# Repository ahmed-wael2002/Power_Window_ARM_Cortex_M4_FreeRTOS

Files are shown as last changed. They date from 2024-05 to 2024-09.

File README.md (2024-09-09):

# Power Window Control System

### 🚗 Project Overview
This project showcases a **Power Window Control System** designed for modern vehicles using the **Tiva C microcontroller** and **FreeRTOS**. The system is scalable, configurable, and integrates various functionalities such as manual and automatic window control, obstacle detection, and safety features. It ensures compatibility across different vehicle models.

### ✨ Key Features
- **Manual & Automatic Control:**
  - **Manual Mode:** Continuous press for precise window control.
  - **Automatic Mode:** One-touch for full open/close functionality.
- **Driver and Passenger Control Board:**
  - Provides window control from driver control board (higher priority) or passenger control board.
- **Window Lock Function:**
  - Locks all windows except the driver's for enhanced security.
- **Jam Protection:**
  - Detects obstacles during the one-touch auto-close operation then retreats the window for safety.
- **Highly Configurable:**
  - Provides manual configuration through MACROS for adapting the project into any hardware architecture.
- **Templates:**
  - Provides sample demo project for easier integration.

 ---

### ✨ Technologies Used
- FreeRTOS (Project built on ARM Keil)
- TM4C123GH6PM (Tiva C Launchpad - ARM Cortex M4)

---

### 🛠️ System Architecture
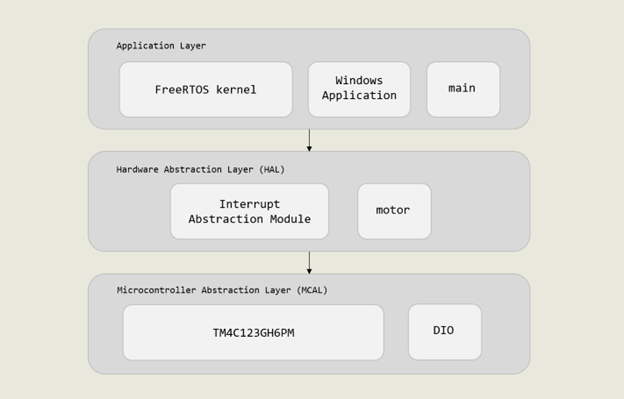
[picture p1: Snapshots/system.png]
System Diagram


---

### 🔧 Configuration
1- Edit the system configurations in Windows.h (Passenger Control GPIO - Driver Control GPIO - Motor GPIO - etc.) as illustrated in the following screenshot.
2- Rebuild the system.
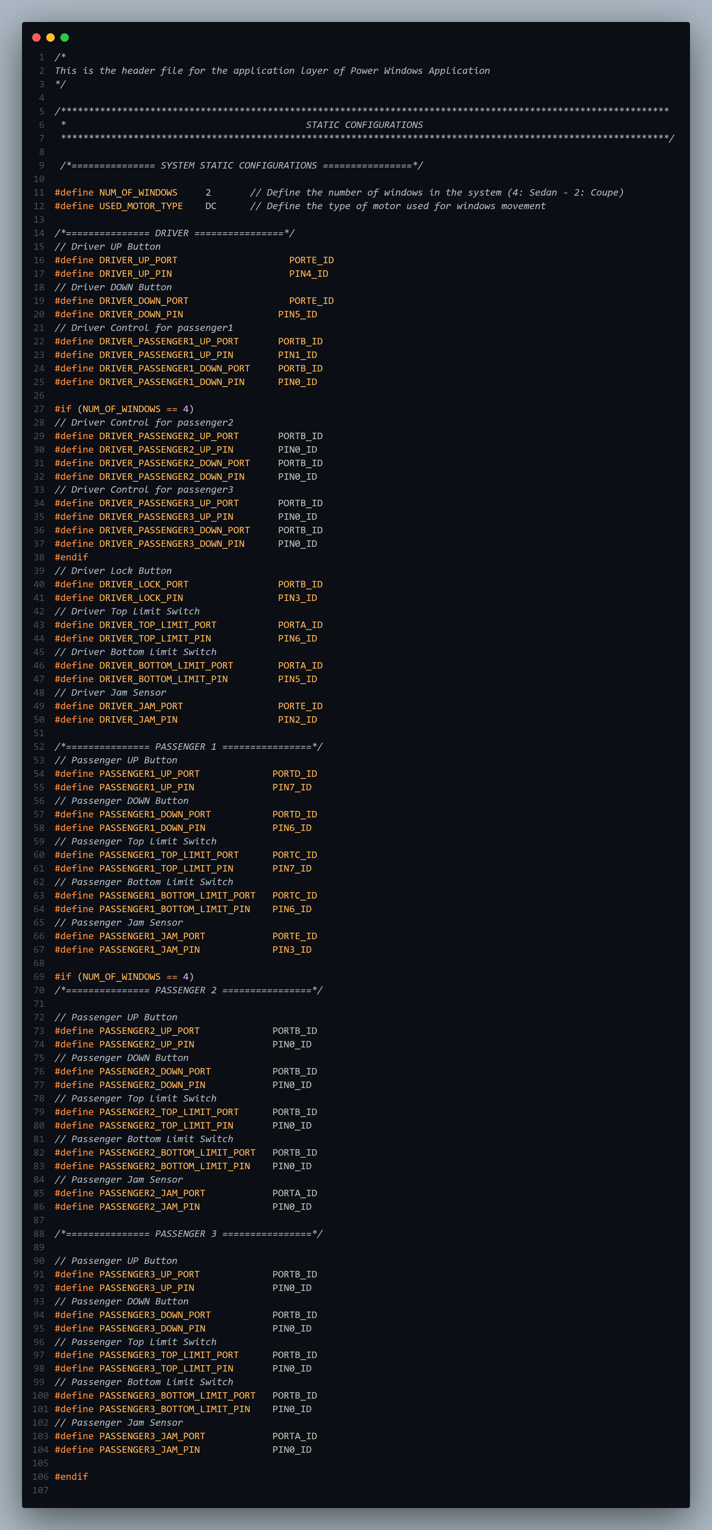
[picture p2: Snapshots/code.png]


--- 

### 📂 Additional Resources
- **[📹 Video Demonstration & Documentation](https://drive.google.com/file/d/1O1Iedp_n3LcsQSbOaQz3eCcksW22hzNp/view?usp=sharing)**
- **[💻 GitHub Repository](https://github.com/ahmed-wael2002/Power_Window_ARM_Cortex_M4_FreeRTOS)**

For more detailed documentation and code examples, visit the [GitHub repository](https://github.com/ahmed-wael2002/Power_Window_ARM_Cortex_M4_FreeRTOS).

---

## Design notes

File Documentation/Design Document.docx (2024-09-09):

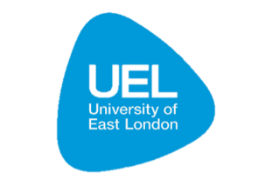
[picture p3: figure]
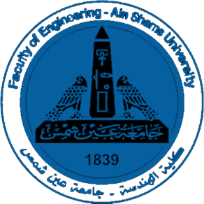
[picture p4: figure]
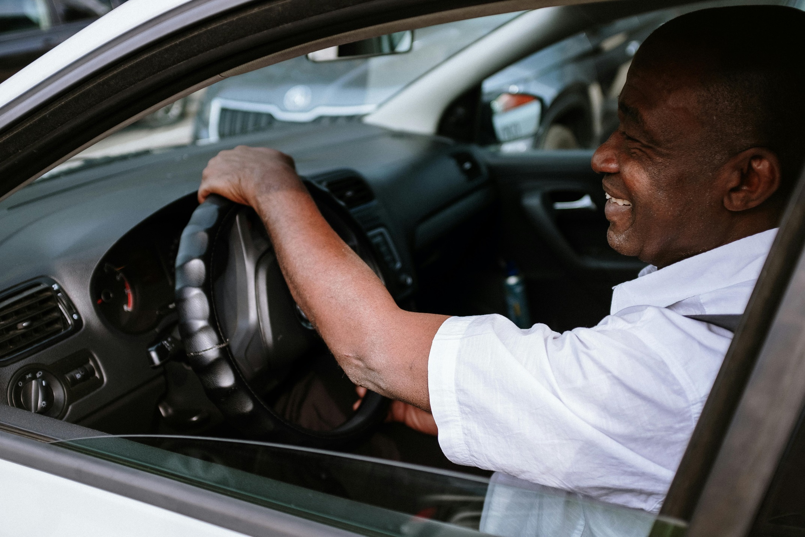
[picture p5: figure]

POWER WINDOW CONTROL SYSTEM using Tiva C running FreeRTOS

Real-time and Embedded Systems Design- CSE411

Submitted to

Prof. Sherif Hammad - Eng. Ayman Baharia

Team: 21

Ahmed Wael Ibrahim Mohamed | 20P3343
Mustafa Usama Abdelrahman | 20P5556
Ahmed Sameh Mahmoud Nabieh | 20P2914
Farah Ahmed Abdelrehim Tharwat | 20P1269
Salma Mohamed Elsoly | 20P6375

# List of Figures

Table 1: Sample main function 7

Project files, video demonstration and Documentation in rar file format:

https://drive.google.com/file/d/1O1Iedp_n3LcsQSbOaQz3eCcksW22hzNp/view?usp=sharing

Github Repository of the project:

ahmed-wael2002/Power_Window_ARM_Cortex_M4_FreeRTOS (github.com) (https://github.com/ahmed-wael2002/Power_Window_ARM_Cortex_M4_FreeRTOS)

# Introduction

In the realm of modern vehicle technology, the Power Window Control System stands out as a pivotal component, elevating passenger convenience and safety. Our endeavor centers on crafting a versatile system capable of seamless integration with a spectrum of vehicle systems. Utilizing the Tiva C microcontroller platform and fortified with the scalability of FreeRTOS for task management, our focus lies on developing a solution that is both generic and adaptable. This approach aims to ensure compatibility across different vehicle models, ultimately enhancing the overall passenger experience.

## Project Scope

The primary objectives of our project are as follows:

1. Front Passenger Door Window Implementation: We aim to create a reliable and generic power window system for passengers and driver windows. Both the passenger and driver control panels will have seamless access to window operation.
2. Power Window (Manual and Automatic Functionalities): We aim to provide manual and automatic window movement function with the utilization of simple push-buttons or any cheap available switches.
3. Generic System: We aim to build a configurable, generic and scalable system conforming to industry standards, helping the software system to be installed on different vehicle systems of different designs.
4. FreeRTOS Integration: We aim to build the system over FreeRTOS open-source kernel, to leverage and demonstrate the power of parallelized tasks execution.
5. Limit Switch Implementation: To ensure safe window operation, we will incorporate two limit switches. These switches will prevent the window motor from exceeding the top and bottom limits of the window frame.
6. Obstacle Detection: While a current stall sensor is unnecessary, we will employ a simple push-button mechanism to detect obstructions. If an obstacle is detected during the one-touch auto-close operation, the system will halt the window movement within 0.5 seconds.

## System Basic Features

Our power window control system will offer the following features:

1. Manual Open/Close Function:
  - When the power window switch is continuously pushed or pulled, the window will open or close until the switch is released.
  - This feature provides flexibility for precise window positioning.
2. One-Touch Auto Open/Close Function:
  - A short press of the power window switch will fully open or close the window.
  - Passengers can effortlessly adjust the window position without continuous input.
3. Window Lock Function:
  - Enabling the window lock switch will disable the opening and closing of all windows except the driver’s window.
  - Enhances security and prevents accidental window adjustments by passengers.
4. Jam Protection Function:
  - In case foreign matter obstructs the window during one-touch auto-close operation, the system will automatically stop the window.
  - Within 0.5 seconds, the window will move downward slightly to release the obstruction.

# System Architecture

## Software Components Layout

Our project utilized the industry standard layered architecture as illustrated in the following figure.

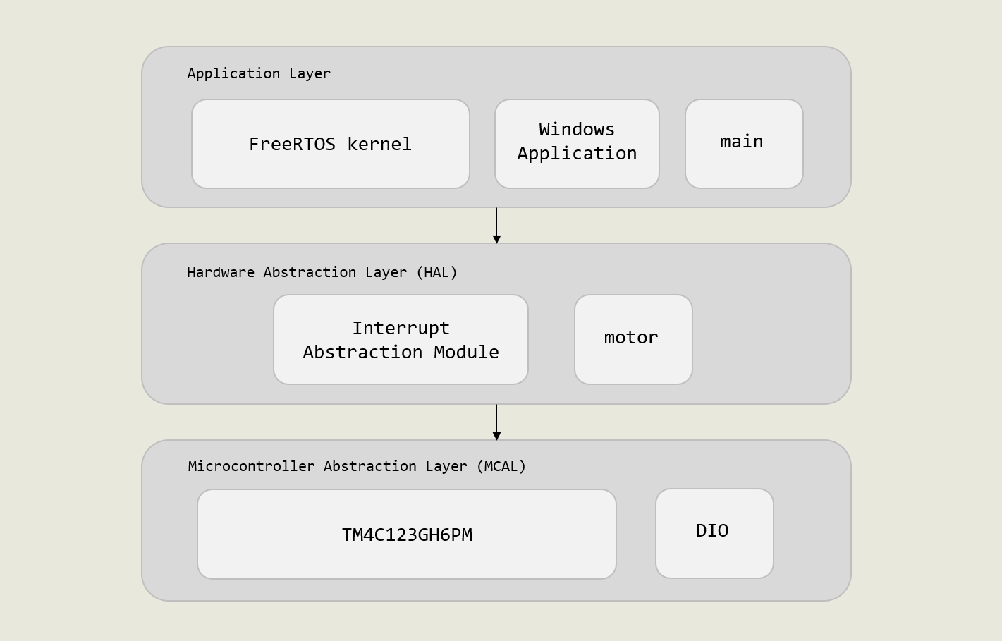
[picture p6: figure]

Figure 1: Layered Architecture Implementation

Application Layer

This is the layer wrapping the actual application code used for building the system. This layer comprises of: FreeRTOS Kernel files, Windows.h header files and main.c main function.

To create a scalable, modular and layered system, windows tasks definitions and functions are declared in a separate software module called windows.h, the main objective is to define the system and task definitions that are loaded into the FreeRTOS kernel for parallel execution. The windows module will be further explained in a later section in this document.

The main.c module initializes the FreeRTOS scheduler, system modules then loads the task definitions into the FreeRTOS application.

Hardware Abstraction Layer

In this layer, we have implemented generic software modules that interface with the underlying hardware components needed for the windows operation: motors and interrupt modules. It is worth noting that the motor driver module is built based on L298N H-bridge Motor Control Board that interfaces with DC Motors. A software modification might be required to re-interface with Stepper motors or any other kind of motors.

## FreeRTOS Tasks Structure

The system was structured with an object-oriented mindset. The system integrator must firstly define the number of windows present in the vehicle then adjust the corresponding static configurations in windows.h header file, this maintains system scalability where the system will define a set of generic parameterized window tasks whose number corresponds to the actual hardware requirements.

In the following diagram, the tasks are divided into: Window Control Tasks, Motor Task and Jamming Tasks. The system integrator can instantiate any number of generic Passenger tasks as will be explained in Window Task, but only 1 Motor and 1 Semaphore Jamming tasks can be instantiated. The motor and jamming tasks were built in a generic form to reduce the overhead of creating multiple tasks for multiple window control panels which might introduce a performance bottleneck in the system.

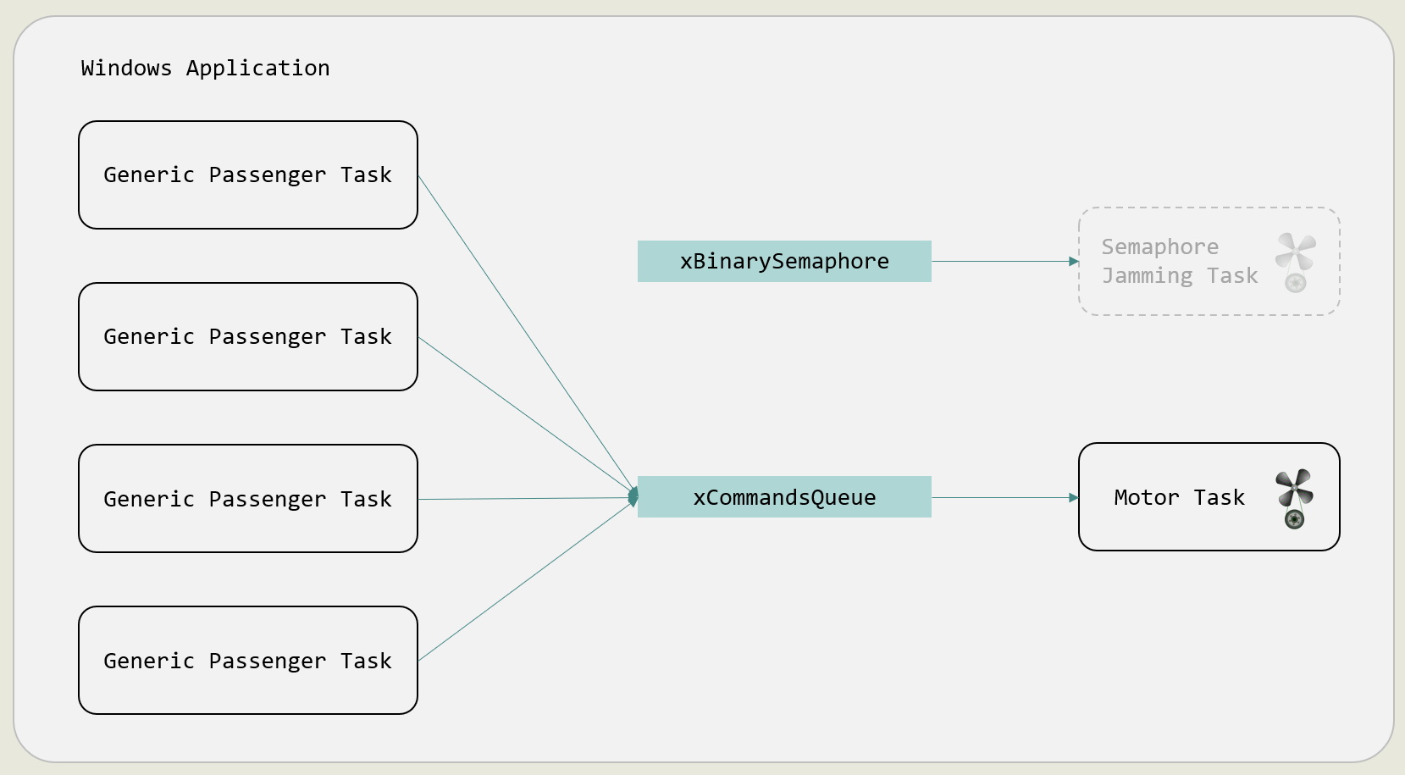
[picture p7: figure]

Figure 2: FreeRTOS Tasks Structure

### Window Task

This is a generic window control task responsible for handling user inputs from the window control panel. The task is generic meaning that the tasks is only defined once but is instantiable to any number of times corresponding to the static configuration “NUM_OF_WINDOWS” found in windows.h. Preferably, this configuration could be NUM_OF_WINDOWS = 2 or 4 to conform to standard vehicle designs.

The task parameters is sent as a structure comprising the necessary input controls GPIO ports and pins, as illustrated in the following snapshot.

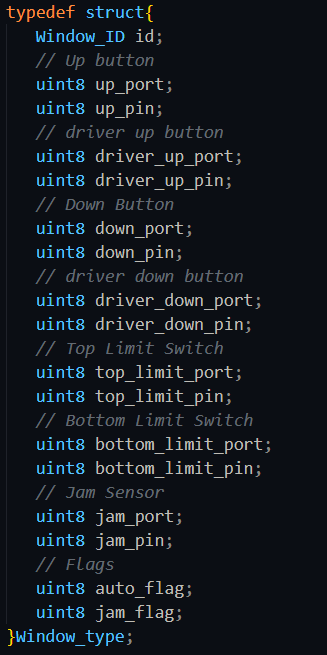
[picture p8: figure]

- Window_id: Is an enumeration used to identify window task, as an example (Driver Task has the id: 0, while Passenger1 Task has the id: 1).
- GPIO ports: These are a group of 8-bit variables that identify the GPIO pin corresponding to each panel input.
- auto_flag, jam_flag: These are Boolean flags used to identify the automatic state of the system and facilitate the jamming operation.

This parameter structure approach facilitates building decoupled tasks, meaning system integrators nor developers are required to define additional functions in the system to add hardware components.

In this sense, the system initialization simply initializes the GPIO pins for panels and fills the structure, an the user can instantiate multiple task functions only by appropriate construction of the parameters.

To automate the task initialization for system integrators, a public array of windows is defined in windows.h and can be externed in the main function to only interate through the array and create a corresponding task as illustrated in the following code example.

Table 1: Sample main function

// Variables are externed from module -- Check for documentation

extern Window_type windows[NUM_OF_WINDOWS];

extern QueueHandle_t xCommandQueue;

extern xSemaphoreHandle xBinarySemaphore;

int main( void )

{

// Initializing Windows GPIO

WINDOW_init();

// Initializing commands queue

xCommandQueue = xQueueCreate(20, sizeof(uint8_t));

// Initializing binary semaphore

vSemaphoreCreateBinary(xBinarySemaphore);

if (xBinarySemaphore != NULL){

// Semaphore is created successfully

for (uint8 i=0; i<NUM_OF_WINDOWS; i++){

// Create Passenger Task (PASSENGER1, PASSENGER2, PASSENGER3

xTaskCreate(

WINDOW_PassengerTask,

"Window Task",

300,

(void *)&windows[i],

1,

NULL

);

}

// Create Motor Task

xTaskCreate(

WINDOW_MotorTask,

"Window Task",

300,

NULL,

1,

NULL

);

// Create jamming semaphore task of higher priority

xTaskCreate(

WINDOW_JammingSemaphoreTask,

"Window Task",

300,

NULL,

3,

NULL

);

// Start the scheduler and run tasks

vTaskStartScheduler();

}

/* If all is well we will never reach here as the scheduler will noe

be running the tasks. If we reach here then it is likely that there was

insufficient heap memory available for a resource to be created */

for(;;);

}

The windows task main aim is to read the user’s input by reading the GPIO pins declared in the parameter structure, process the inputs to define the operation to be executed then communicate a command to the motor task to move interface with the motor hardware. The task communication process is further explained in the Commands and Queues section.

The following features are implemented in this module as follows:

- Manual Control: the GPIO pin is read then vTaskDelay() is called to wait for a specific period of time, then re-read the GPIO pin. A post-delay ON reading on the GPIO pin indicates the user’s continuous press on the switch triggering the manual movement of the windows. It is worth noting that the jamming operation is only accounted for in the automatic operation as defined in the design specifications document.
- Automatic Control: As opposed to Manual Control operation, a post-delay OFF reading indicates the user’s one-touch press which triggers the automatic movement of the windows.
- xQueueSend: The operation command is pushed into the commands queue to be continuously read by the motor task for execution.
- Driver-to-passenger Control: In the parameter structure, a corresponding driver_up_GPIO and driver_down_GPIO where they are also read in the generic task, however, the reading operation is conditional, meaning, it can only be read, if the private global variable g_isLocked is on, in other words, the driver locked the windows operations. This makes the windows only controllable by the driver in case of locked state.
- Limit Switches: Limit switches GPIO parameters set a group of conditions that resets the task operation and force it to send a Motor_stop command to the motor task.

### Motor Task

The motor task simple continuously receives from the commands queue task commands, decodes the commands then call the corresponding function from the motor driver module to interface with the hardware.

### Commands and Queues

A queue is defined to create a communication channel between the window control tasks and the motor tasks to help send/receive commands and execute operations.

The following code snapshot illustrates the basic commands defined in the system (Command definitions can be found in the Operational Macros section in windows.h).

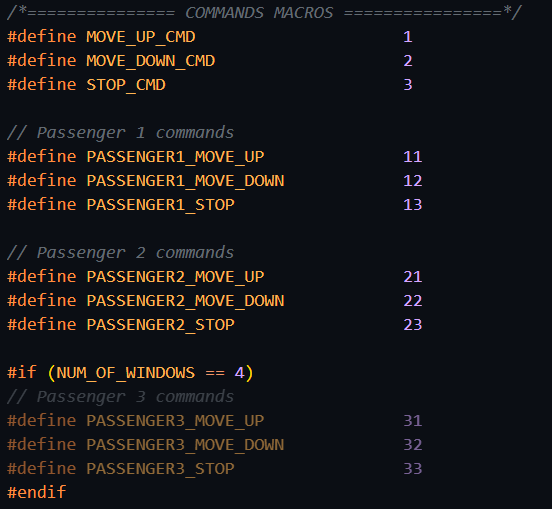
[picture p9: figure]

As discussed in the Window Task section, a reduction in the tasks creation overhead is achieved by creating a single generic Motor task. This is achieved by creating a commands protocol which the motor task could decode and understand which motor to be activated and with which operation.

As discussed also, the parameter structure contain a window_id, which can be used to identify the target motor hardware, our implementation of the command is simple and goes as follows:

command=(window id*10)+command

For example, the command for triggering PASSENGER2 windows of id=2 to move upwards would be as follows:

pass2 move up cmd=(2*10)+1=21

### Semaphores and Jamming

Jamming is considered a safety-critical issue whose priority exceeds all operations of the system, consecutively, the implementation of jamming operation is done using a higher-priority task that directly controls the motors and have access to windows array.

Referring to Figure 2: FreeRTOS Tasks Structure the Jamming task is initially blocked as the semaphore is not given, until the Jamming_ISR defined in windows.c toggles the jam_flag in a corresponding windows array element, after wise, the ISR gives the semaphore to the Jamming task then forces context switching.

The semaphore task then iterates through the array of windows till it finds a window object whose jam_flag is on, it then assesses the auto_flag which is only raised in case of automatic move up operation. If both flags are raised, the Jamming task forces the motor to move in the opposite direction for a statically configured JAM_DELAY_MS then stops the motor. It is worth noting that the Jamming task also checks for bottom_limit_switches to avoid moving the window outside its boundaries. The following code snapshots showcase the implementation of the semaphore task and ISR.

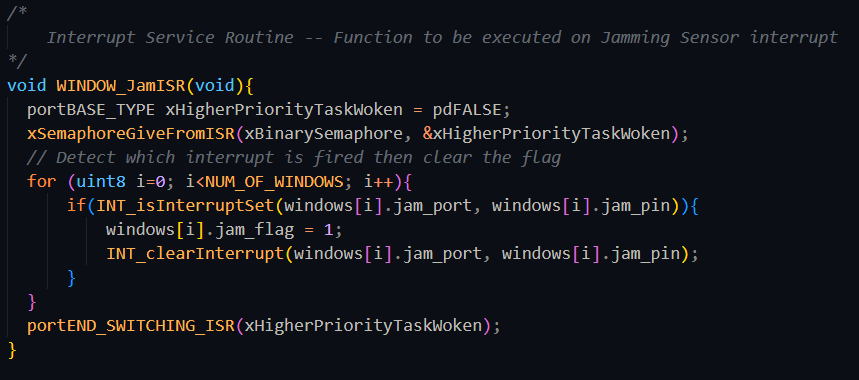
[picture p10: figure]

Figure 3: Jam Interrupt Service Routine

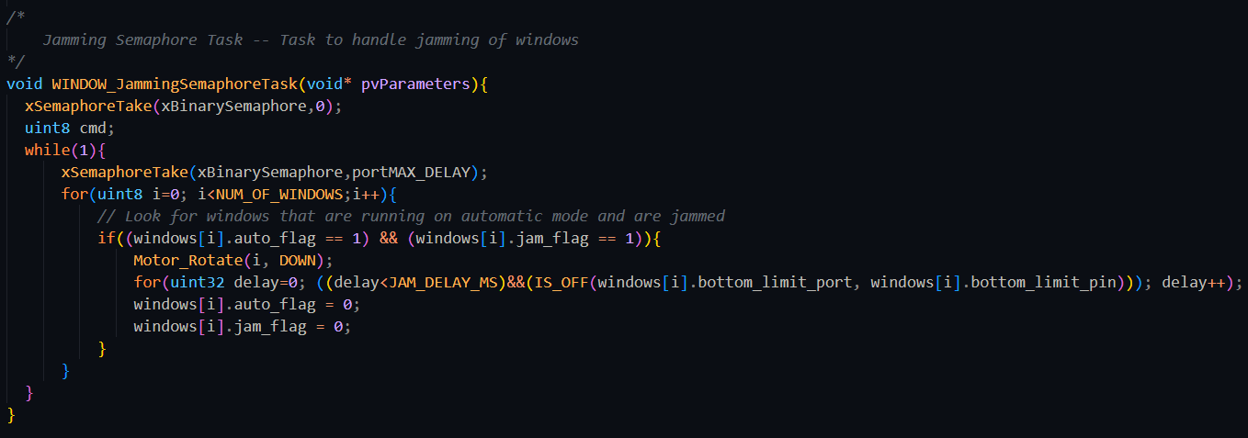
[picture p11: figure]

Figure 4: Jamming semaphore task implementation

# Demonstration

## Hardware Items List

Item Image | Item Name/Code | Functionality

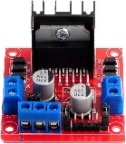
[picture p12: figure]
L298N Motor Drive Controller Board Module Dual H Bridge DC Stepper ForArduino Smart Car Robot UNO MEGA R3 MEGA 2560 ESP32 ESP826

| Dual H-Bridge Motor Driver | Hardware control board that bridges and facilitates the connection of the DC motors with Tiva C board

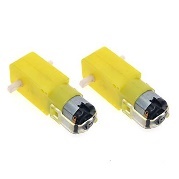
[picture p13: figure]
Mini DC Gearbox Motors Pair (2 Motors) With Back Shaft

| Mini DC Gearbox Motors with Back Shaft | DC Motors used to move windows in both directions, a gearbox is used to reduce the RPM speed of motors with no software intervention

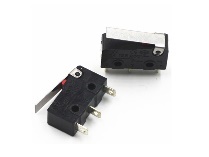
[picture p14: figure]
Micro Switch - MS2

| Micro Limit Switches | Used to signal whether the window reached the maximum height limit or the maximum depth limit

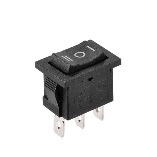
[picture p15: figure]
SW4 - ON/OFF/ON Switch 3 pin

| 3-level Rocker Switch | Used in the window control panel to signal up/down commands

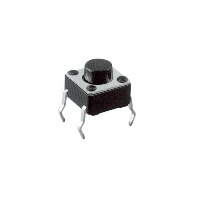
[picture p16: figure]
Press 4pin 6x6x4.5 mm Tack Switch

| Push button | Used to emulate GPIO input for Jamming Stall Sensors

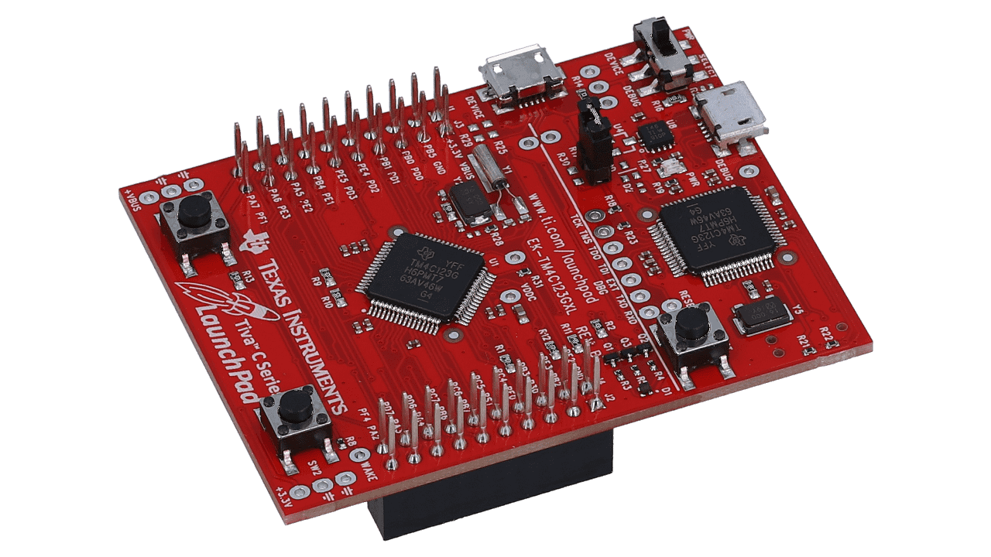
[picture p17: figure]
EK-TM4C123GXL Evaluation board | TI.com

| Tiva C Launchpad | Arm Cortex M4 – based microcontroller

## Circuit Wiring

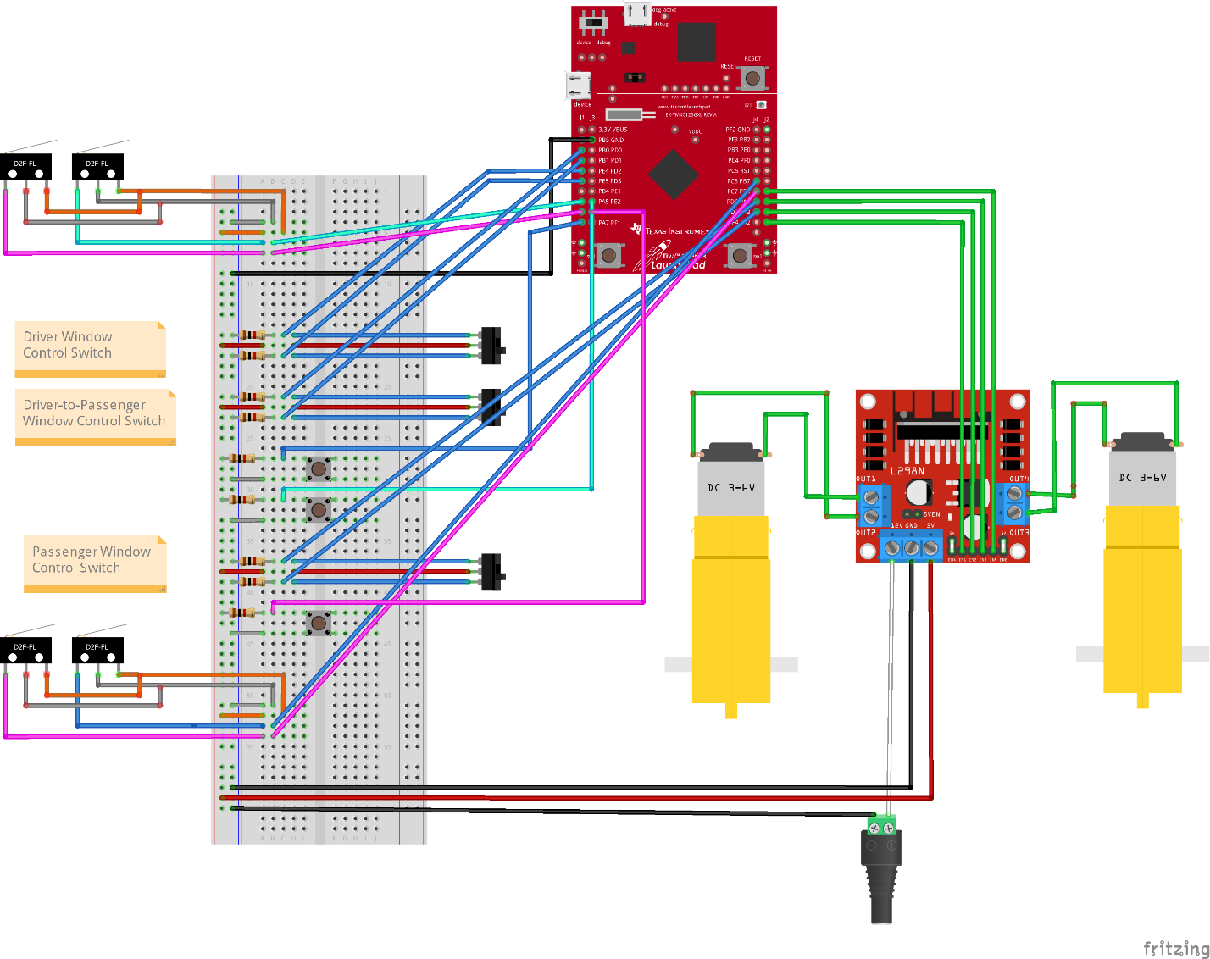
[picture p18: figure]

Figure 5: Demo project circuit wiring using Fritzing

## Software System Integration

System Configurations are adjusted in the statics configurations section in windows.h header file as follows

1. Firstly, adjust NUM_OF_WINDOWS = 2. In this demo project we will use the 2-seat vehicle design with only 1 Driver and 1 Passenger Control panels.
2. Adjust all ports and pins accordingly
3. Use the code sample in Window Task section.

The following are the static configurations used in the demo project.

/*=============== SYSTEM STATIC CONFIGURATIONS ================*/

#define NUM_OF_WINDOWS 2 // Define the number of windows in the system (4: Sedan - 2: Coupe)

#define USED_MOTOR_TYPE DC // Define the type of motor used for windows movement

/*=============== DRIVER ================*/

// Driver UP Button

#define DRIVER_UP_PORT PORTE_ID

#define DRIVER_UP_PIN PIN4_ID

// Driver DOWN Button

#define DRIVER_DOWN_PORT PORTE_ID

#define DRIVER_DOWN_PIN PIN5_ID

// Driver Control for passenger1

#define DRIVER_PASSENGER1_UP_PORT PORTB_ID

#define DRIVER_PASSENGER1_UP_PIN PIN1_ID

#define DRIVER_PASSENGER1_DOWN_PORT PORTB_ID

#define DRIVER_PASSENGER1_DOWN_PIN PIN0_ID

// Driver Lock Button

#define DRIVER_LOCK_PORT PORTB_ID

#define DRIVER_LOCK_PIN PIN3_ID

// Driver Top Limit Switch

#define DRIVER_TOP_LIMIT_PORT PORTA_ID

#define DRIVER_TOP_LIMIT_PIN PIN6_ID

// Driver Bottom Limit Switch

#define DRIVER_BOTTOM_LIMIT_PORT PORTA_ID

#define DRIVER_BOTTOM_LIMIT_PIN PIN5_ID

// Driver Jam Sensor

#define DRIVER_JAM_PORT PORTE_ID

#define DRIVER_JAM_PIN PIN2_ID

/*=============== PASSENGER 1 ================*/

// Passenger UP Button

#define PASSENGER1_UP_PORT PORTD_ID

#define PASSENGER1_UP_PIN PIN7_ID

// Passenger DOWN Button

#define PASSENGER1_DOWN_PORT PORTD_ID

#define PASSENGER1_DOWN_PIN PIN6_ID

// Passenger Top Limit Switch

#define PASSENGER1_TOP_LIMIT_PORT PORTC_ID

#define PASSENGER1_TOP_LIMIT_PIN PIN7_ID

// Passenger Bottom Limit Switch

#define PASSENGER1_BOTTOM_LIMIT_PORT PORTC_ID

#define PASSENGER1_BOTTOM_LIMIT_PIN PIN6_ID

// Passenger Jam Sensor

#define PASSENGER1_JAM_PORT PORTE_ID

#define PASSENGER1_JAM_PIN PIN3_ID

A system integrator can scale up the demo project by changing the value NUM_OF_WINDOWS macro to 4 then adjust the appropriate configurations for the GPIO pins.

In addition, one can use the sample code as the main code to initialize tasks and system hardware enlisted in Table 1: Sample main function.

2 Real-time and Embedded Systems Design – CSE411

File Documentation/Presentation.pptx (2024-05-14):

## Power window using freeRTOS

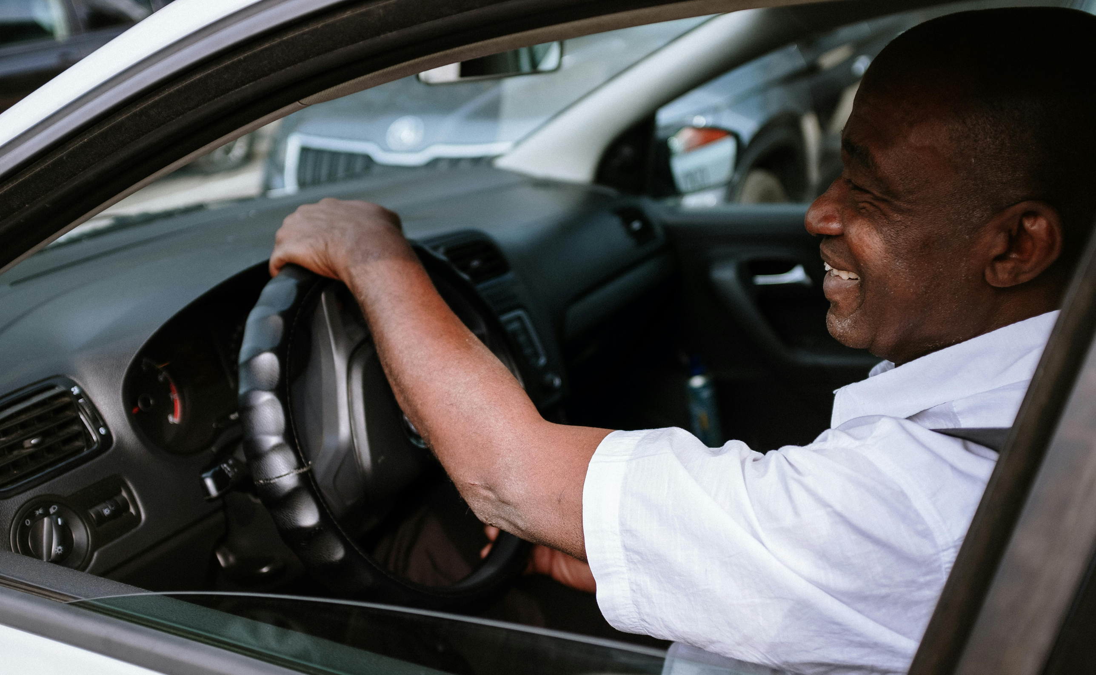
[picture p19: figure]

## Team 21

Ahmed Wael Ibrahim – 20P3343
Mustafa Usama Abdelrahman – 20P5556
Ahmed Sameh Mahmoud Nabieh – 20P2914
Farah Ahmed Abdelrehim Tharwat – 20P1269
Salma Mohamed Elsoly – 20P6375

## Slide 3

Application Layer

Hardware Abstraction Layer (HAL)

FreeRTOS kernel

Windows Application

main

Interrupt Abstraction Module

motor

Microcontroller Abstraction Layer (MCAL)

TM4C123GH6PM

DIO

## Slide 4

Windows Application

Generic Passenger Task

Semaphore Jamming Task

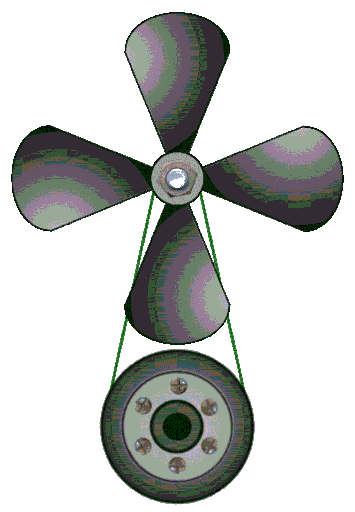
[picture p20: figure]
Propeller Motor Air - Free GIF on Pixabay - Pixabay

Generic Passenger Task

xBinarySemaphore

Generic Passenger Task

Motor Task

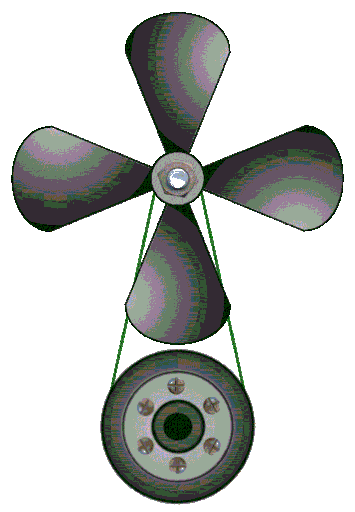
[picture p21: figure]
Propeller Motor Air - Free GIF on Pixabay - Pixabay

xCommandsQueue

Generic Passenger Task

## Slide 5

Windows Application

Generic Passenger Task

Semaphore Jamming Task

Generic Passenger Task

xBinarySemaphore

Generic Passenger Task

Motor Task

xCommandsQueue

Generic Passenger Task

## Code implementation

## Demo project

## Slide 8

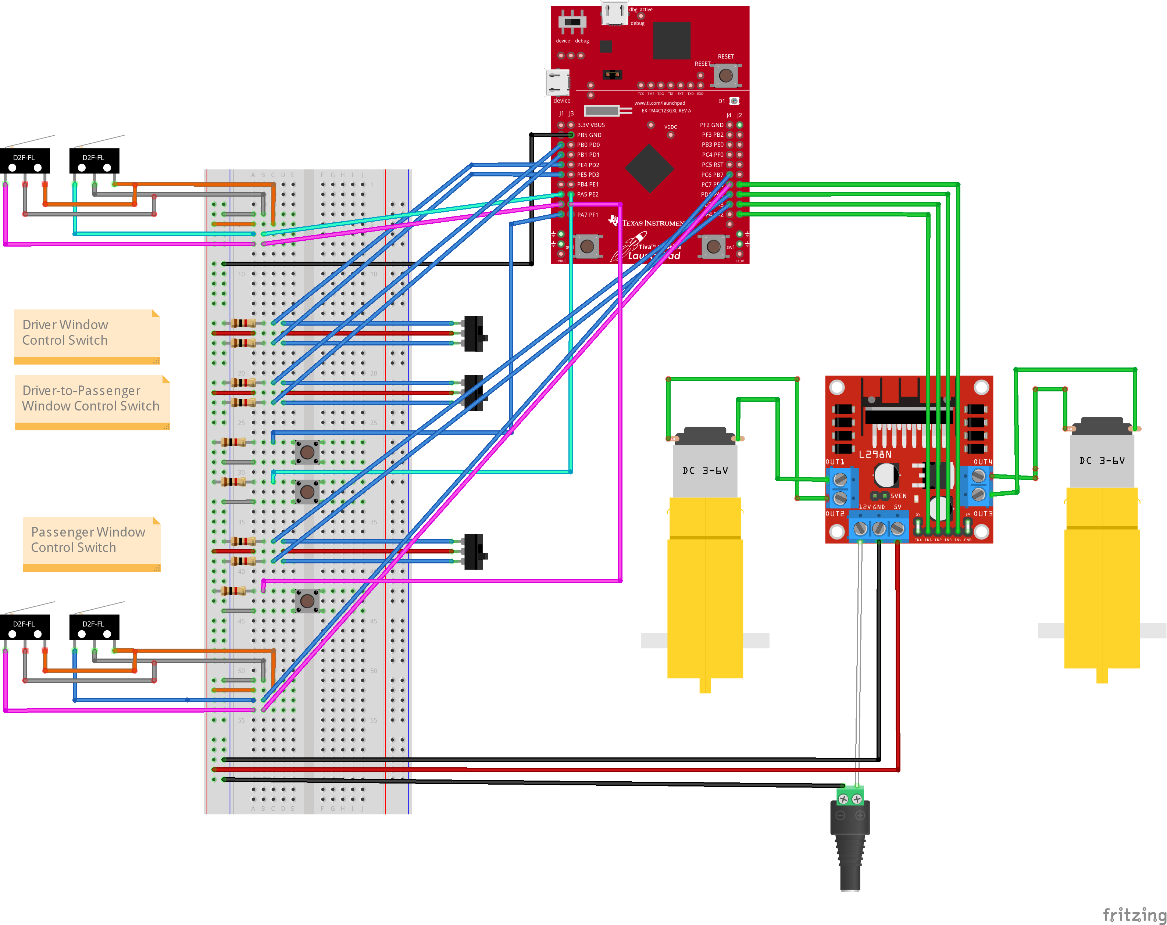
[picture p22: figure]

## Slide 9

- Two panels are installed to control the passenger’s window?
- FreeRTOS is used in the project implementation?
- Implementation of 2 limit switches to limit the window motor from top and bottom limits of the window?
- When the power window switch is pushed or pulled continuously, the window opens or closes until the switch is released?
- When the power window switch is pushed or pulled shortly, the window fully opens or closes?
- When the window lock switch is turned on, the opening and closing of all windows except the driver’s window is disabled?
- Jam Protection is implemented?
- Queues are used in the project implementation?
- Semaphores/Mutex are used in the project implementation?
- Documentation project is made?

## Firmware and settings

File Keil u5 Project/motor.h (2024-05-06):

/*
 * motor.h
 *
 *  Created on: Apr 24, 2024
 *      Author: Ahmed Wael
 */

#ifndef MOTOR_H_
#define MOTOR_H_

#include "types.h"
#include "DIO.h"

/* 
This is header file declares a set of functions to control 2 DC motors 
by interfacing with L298N Motor Driver Module which allows simultaneous control of 2 motors.
The driver module is controlled by 3 pins:
1- Enable 1 pin: to enable the first motor
2- Input 1,2 pins: Control the rotation direction of the first motor
3- Enable 2 pin: to enable the second motor
4- Input 3,4 pins: Control the rotation direction of the second motor
*/

/*************************************************************************************************************
  			                                MACROS DEFINITIONS
 *************************************************************************************************************/

/*=============== SYSTEM STATIC CONFIGURATIONS ================*/
#define NUM_OF_MOTORS		2
#define TYPE_OF_MOTORS		DC


/*=============== OPERATIONAL MACROS ================*/





/*=============== MOTORS GPIO ================*/

/* Defining Enable pin for Motor
 * In case of a variable speed driver:
 * 	This pin should be connected to timer PWM output pin
 */

// Controlling First Motor
#define MOTOR1_EN_PORT 		PORTA_ID
#define MOTOR1_EN_PIN 		PIN4_ID
#define MOTOR1_IN1_PORT 	PORTA_ID
#define MOTOR1_IN1_PIN 		PIN2_ID
#define MOTOR1_IN2_PORT 	PORTA_ID
#define MOTOR1_IN2_PIN 		PIN3_ID

// Controlling Second Motor
#define MOTOR2_EN_PORT 		PORTD_ID
#define MOTOR2_EN_PIN 		PIN6_ID
#define MOTOR2_IN1_PORT		PORTA_ID
#define MOTOR2_IN1_PIN		PIN4_ID
#define MOTOR2_IN2_PORT		PORTB_ID
#define MOTOR2_IN2_PIN		PIN6_ID

#if (NUM_OF_MOTORS == 4)
// Controlling Third Motor
#define MOTOR3_EN_PORT 		PORTB_ID
#define MOTOR3_EN_PIN 		PIN3_ID
#define MOTOR3_IN1_PORT 	PORTB_ID
#define MOTOR3_IN1_PIN 		PIN0_ID
#define MOTOR3_IN2_PORT 	PORTB_ID
#define MOTOR3_IN2_PIN 		PIN1_ID

// Controlling Fourth Motor
#define MOTOR4_EN_PORT 		PORTB_ID
#define MOTOR4_EN_PIN 		PIN4_ID
#define MOTOR4_IN1_PORT		PORTD_ID
#define MOTOR4_IN1_PIN		PIN0_ID
#define MOTOR4_IN2_PORT		PORTD_ID
#define MOTOR4_IN2_PIN		PIN1_ID
#endif

/******************************************
 * 			 TYPES DEFINITIONS
 ******************************************/
/*
 * This enum is used to define the direction of rotation of the motor
 * 1- OFF			: IN1=0, IN2=0
 * 2- ANTICLOCKWISE	: IN1=0, IN2=1
 * 3- CLOCKWISE		: IN1=1, IN2=0
 */
typedef enum{
	OFF,			/* 00 */
	ANTICLOCKWISE, 	/* 01 */
	CLOCKWISE		/* 10 */
}Motor_Direction;

typedef enum{
	MOTOR1,
	MOTOR2,
	MOTOR3,
	MOTOR4
}Motor_ID;


/******************************************
 * 			FUNCTION PROTOTYPES
 ******************************************/
void Motor_init(void);
void Motor_Rotate(Motor_ID motor, Motor_Direction direction);


#endif /* MOTOR_H_ */

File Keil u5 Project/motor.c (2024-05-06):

/*
 * motor.c
 *
 *  Created on: Apr 24, 2024
 *      Author: Wael
 */

 // This is a simple implementation for the motor driver
 // The Power Window project requirements only need constant rotation speed so PWM control will not be implemented
 // Such reduction is necessary to avoid unnecessary usage of timers and PWM controls
 // Ensure jumper is placed on the Enable pins to allow max speed operation

/****** PWM control can be added in future implementations calling for variable speed ******/

#include "motor.h"


/*
 * This function initializes the DC motors by setting up the direction and state of the motor pins.
 * It also ensures that all the motor pins are initially set to the off state.
 */
void Motor_init(void){
	// Motor 1 - inits
	//DIO_Init(MOTOR1_EN_PORT, MOTOR1_EN_PIN, PIN_OUTPUT);
	DIO_Init(MOTOR1_IN1_PORT, MOTOR1_IN1_PIN, PIN_OUTPUT);
	DIO_Init(MOTOR1_IN2_PORT, MOTOR1_IN2_PIN, PIN_OUTPUT);
	//DIO_writePin(MOTOR1_EN_PORT, MOTOR1_EN_PIN, LOGIC_LOW);
	DIO_writePin(MOTOR1_IN1_PORT, MOTOR1_IN1_PIN, LOGIC_LOW);
	DIO_writePin(MOTOR1_IN2_PORT, MOTOR1_IN2_PIN, LOGIC_LOW);
	
	// Motor 2 - inits
	//DIO_Init(MOTOR2_EN_PORT, MOTOR2_EN_PIN, PIN_OUTPUT);
	DIO_Init(MOTOR2_IN1_PORT, MOTOR2_IN1_PIN, PIN_OUTPUT);
	DIO_Init(MOTOR2_IN2_PORT, MOTOR2_IN2_PIN, PIN_OUTPUT);
	//DIO_writePin(MOTOR2_EN_PORT, MOTOR2_EN_PIN, LOGIC_LOW);
	DIO_writePin(MOTOR2_IN1_PORT, MOTOR2_IN1_PIN, LOGIC_LOW);
	DIO_writePin(MOTOR2_IN2_PORT, MOTOR2_IN2_PIN, LOGIC_LOW);
		
	#if (NUM_OF_MOTORS == 4)
	// Motor 3 - inits
	DIO_Init(MOTOR3_EN_PORT, MOTOR3_EN_PIN, PIN_OUTPUT);
	DIO_Init(MOTOR3_IN1_PORT, MOTOR3_IN1_PIN, PIN_OUTPUT);
	DIO_Init(MOTOR3_IN2_PORT, MOTOR3_IN2_PIN, PIN_OUTPUT);
	DIO_writePin(MOTOR3_EN_PORT, MOTOR3_EN_PIN, LOGIC_LOW);
	DIO_writePin(MOTOR3_IN1_PORT, MOTOR3_IN1_PIN, LOGIC_LOW);
	DIO_writePin(MOTOR3_IN2_PORT, MOTOR3_IN2_PIN, LOGIC_LOW);
	
	// Motor 4 - inits
	DIO_Init(MOTOR4_EN_PORT, MOTOR4_EN_PIN, PIN_OUTPUT);
	DIO_Init(MOTOR4_IN1_PORT, MOTOR4_IN1_PIN, PIN_OUTPUT);
	DIO_Init(MOTOR4_IN2_PORT, MOTOR4_IN2_PIN, PIN_OUTPUT);
	DIO_writePin(MOTOR4_EN_PORT, MOTOR4_EN_PIN, LOGIC_LOW);
	DIO_writePin(MOTOR4_IN1_PORT, MOTOR4_IN1_PIN, LOGIC_LOW);
	DIO_writePin(MOTOR4_IN2_PORT, MOTOR4_IN2_PIN, LOGIC_LOW);
	#endif
}

/*
 * This function rotates the DC motor in the specified direction.
 * It takes two parameters: the motor ID and the direction.
 * The motor ID can be either MOTOR1 or MOTOR2.
 * The direction can be OFF, ANTICLOCKWISE, or CLOCKWISE.
 */
void Motor_Rotate(Motor_ID motor, Motor_Direction direction){
	switch(motor){
		case MOTOR1:
			if (direction == OFF){
				DIO_writePin(MOTOR1_IN1_PORT, MOTOR1_IN1_PIN, LOGIC_LOW);
				DIO_writePin(MOTOR1_IN2_PORT, MOTOR1_IN2_PIN, LOGIC_LOW);
			}
			else if (direction == ANTICLOCKWISE){
				DIO_writePin(MOTOR1_IN1_PORT, MOTOR1_IN1_PIN, LOGIC_LOW);
				DIO_writePin(MOTOR1_IN2_PORT, MOTOR1_IN2_PIN, LOGIC_HIGH);
			}
			else if (direction == CLOCKWISE){
				DIO_writePin(MOTOR1_IN1_PORT, MOTOR1_IN1_PIN, LOGIC_HIGH);
				DIO_writePin(MOTOR1_IN2_PORT, MOTOR1_IN2_PIN, LOGIC_LOW);
			}
		break;

		case MOTOR2:
			if (direction == OFF){
				DIO_writePin(MOTOR2_IN1_PORT, MOTOR2_IN1_PIN, LOGIC_LOW);
				DIO_writePin(MOTOR2_IN2_PORT, MOTOR2_IN2_PIN, LOGIC_LOW);
			}
			else if (direction == ANTICLOCKWISE){
				DIO_writePin(MOTOR2_IN1_PORT, MOTOR2_IN1_PIN, LOGIC_LOW);
				DIO_writePin(MOTOR2_IN2_PORT, MOTOR2_IN2_PIN, LOGIC_HIGH);
			}
			else if (direction == CLOCKWISE){
				DIO_writePin(MOTOR2_IN1_PORT, MOTOR2_IN1_PIN, LOGIC_HIGH);
				DIO_writePin(MOTOR2_IN2_PORT, MOTOR2_IN2_PIN, LOGIC_LOW);
			}
		break;

		#if (NUM_OF_MOTORS == 4)
		case MOTOR3:
			if (direction == OFF){
				DIO_writePin(MOTOR3_IN1_PORT, MOTOR3_IN1_PIN, LOGIC_LOW);
				DIO_writePin(MOTOR3_IN2_PORT, MOTOR3_IN2_PIN, LOGIC_LOW);
			}
			else if (direction == ANTICLOCKWISE){
				DIO_writePin(MOTOR3_IN1_PORT, MOTOR3_IN1_PIN, LOGIC_LOW);
				DIO_writePin(MOTOR3_IN2_PORT, MOTOR3_IN2_PIN, LOGIC_HIGH);
			}
			else if (direction == CLOCKWISE){
				DIO_writePin(MOTOR3_IN1_PORT, MOTOR3_IN1_PIN, LOGIC_HIGH);
				DIO_writePin(MOTOR3_IN2_PORT, MOTOR3_IN2_PIN, LOGIC_LOW);
			}
		break;

		case MOTOR4:
			if (direction == OFF){
				DIO_writePin(MOTOR4_IN1_PORT, MOTOR4_IN1_PIN, LOGIC_LOW);
				DIO_writePin(MOTOR4_IN2_PORT, MOTOR4_IN2_PIN, LOGIC_LOW);
			}
			else if (direction == ANTICLOCKWISE){
				DIO_writePin(MOTOR4_IN1_PORT, MOTOR4_IN1_PIN, LOGIC_LOW);
				DIO_writePin(MOTOR4_IN2_PORT, MOTOR4_IN2_PIN, LOGIC_HIGH);
			}
			else if (direction == CLOCKWISE){
				DIO_writePin(MOTOR4_IN1_PORT, MOTOR4_IN1_PIN, LOGIC_HIGH);
				DIO_writePin(MOTOR4_IN2_PORT, MOTOR4_IN2_PIN, LOGIC_LOW);
			}
		break;

		#endif 

	}
}

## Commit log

2024-05-03 First Commit -- Not Working Yet
    [DIO.c, DIO.h, int.c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]
2024-05-04 Built-Code: Re-implemented modules + Enhanced interrupts module
2024-05-04 Updated Motor Driver APIs -- Added Blank Driver Task
2024-05-06 Successful Build + Test -- 2 Passenger tasks working in parallel + optimized power saving mode
2024-05-09 -- Added INT_clearInterrupt, INT_isInterruptSet functions in interrupt module, fixed jamming semaphore task, final working project v.1
    [int.c, int.h, main.c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]
2024-05-10 -- Added Documentation + Presentation -- Fixed Driver Control Lock Issue -- Fixed ON/OFF Switch Lock Issue (Interrupt Module needs revision)
    [Circuit.fzz]
